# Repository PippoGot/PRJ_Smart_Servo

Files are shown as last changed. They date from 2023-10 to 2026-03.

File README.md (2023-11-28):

# Smart Servo Project
----------------------------------------------------------------

The scope of this repository is to design a new controller board for the MG996R
hobby servo, in order to improve position accuracy and performance.

In particular, the goal is to:

- Implement a more accurate position controller;

- Implement a current controller to limit stall overheating;

- Implement a I2C interface to control the servo, for:
    + current and position readings;
    + flexible and overwritable PID controller & threshold values;
    + calibration routine to estimate motor parameter;
    + possibility of daisy-chaining more servos using a limited number of ports;

More useful things to have are:

- Thermal safety shutdown;

----------------------------------------------------------------
## Folder Structure:

- "DATASHEETS": contains all of the datasheets for the components used,
both in the original controller board and in the new developed board;

- "default servo control board": contains the KiCAD files of the reverse engineered
original servo controller board;

- "MODELS & SIMULATIONS": contains the Simulink and LTSpice models, as well as the
Matlab scripts for parameters and controller tuning;

- "SOURCE": contains all the code for the microcontroller;

- "STM32 PDFs & DATASHEET": contains the documentation of the microcontroller
applied to the board, as well as some useful PDFs for making and programming
embedded projects using the microcontroller itself;

- "STM32F103C8T6 minimum board": contains the KiCAD files of a minimum board
for any embedded project using that specific microcontroller;

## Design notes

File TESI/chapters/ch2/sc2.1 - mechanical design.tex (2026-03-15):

\section{Structural Design}

The robotic leg is conceived as a three degrees of freedom (3-DOF) manipulator, a common simplification
of an insect's limb, designed to provide sufficient motion versatility within a robust and manageable structure.
The kinematic chain consists of three rigid links — Coxa, Femur, and Tibia — connected sequentially by three
revolute joints (from the robot's body toward the end-effector, as shown in Figure \ref{fig:hexapod_leg}):

\begin{itemize}
    \item \textbf{Hip Joint} ($q_1$): Connects the robot's body to the Coxa link and primarily controls the
        \textbf{yaw} motion of the leg, responsible for the lateral sweep relative to the body's longitudinal axis.
    \item \textbf{Knee Joint} ($q_2$): Connects the Coxa link to the Femur link and controls the
        \textbf{primary pitch} motion, enabling the lifting and lowering of the leg structure.
    \item \textbf{Ankle Joint} ($q_3$): Connects the Femur link to the Tibia link and controls the
        \textbf{secondary pitch} motion, significantly influencing the height and reach of the Foot (end-effector).
\end{itemize}

This configuration, is widely adopted in hexapod designs as it provides an optimal balance between complexity
and dexterity, allowing for effective gait planning and stable locomotion on various surfaces.

\begin{figure}[htbp]
    \centering
    
    \caption{Schematic Representation of the Mechanical Limb}
    \label{fig:hexapod_leg}
\end{figure}

\subsection{Limb Parametrization and Forward Kinematics}
\label{sec:dh_params}

The Denavit--Hartenberg (DH) convention \cite{denavit1955kinematic, siciliano2009robotics} is the standard
mathematical tool for describing the spatial relationships and defining the minimal parameter set required for
kinematic analysis of serial manipulators. By rigidly attaching coordinate frames to each link, DH enables a
standardized description of the link geometry and joint configuration.

The assignment of these frames follows a systematic methodology designed to isolate the four key parameters.
For a kinematic chain starting from a base frame $\{0\}$, a coordinate frame $\{i\}$ is rigidly attached to
link $i$. The most important rule is that the $z_i$-axis is placed along the axis of actuation (either
rotation or translation) for joint $i$. The $x_i$-axis is then constructed along the common normal connecting
$z_{i-1}$ (the previous joint axis) to $z_i$ (the current joint axis), with the origin of frame $\{i\}$
located at the intersection of $x_i$ and $z_i$. Finally, the $y_i$ axis is simply set to complete a
right-handed coordinate system.

Using this precise, rule-based placement of axes the entire transformation from frame $\{i\}$ to frame $\{i+1\}$
can now be described by a sequence of four fundamental operations tied directly to this geometry: the Link Length
($a_i$), Link Twist ($\alpha_i$), Link Offset ($d_i$), and the Joint Angle ($\theta_i$) (see Figure
\ref{fig:denavit_hartenberg}).

\begin{figure}[htbp]
    \centering
    
    \caption{Illustration of Denavit--Hartenberg Convention Parameters}
    \label{fig:denavit_hartenberg}
\end{figure}

The homogeneous transformation matrix, $T_{i}^{i+1}$, from frame $\{i\}$ to frame $\{i+1\}$, is given by:

\begin{equation}
    T_{i}^{i+1} = R_x(\alpha_i) \cdot T_x(a_i) \cdot R_z(\theta_i) \cdot T_z(d_i) =
    \begin{bmatrix}
        c_{\theta} & -s_{\theta} & 0 & a \\
        s_{\theta} c_{\alpha} & c_{\theta} c_{\alpha} & -s_{\alpha} & -ds_{\alpha} \\
        s_{\theta} s_{\alpha} & c_{\theta} s_{\alpha} & c_{\alpha} & dc_{\alpha} \\
        0 & 0 & 0 & 1
    \end{bmatrix}
\end{equation}

where the contracted notation $c_x = \cos(x), s_x = \sin(x)$ was used, while the overall transformation from
the base frame $\{b\}$ to the end-effector frame $\{e\}$, $T_b^e$, which is the Forward Kinematics solution,
is computed by the serial multiplication of these individual matrices:

\begin{equation}
    T_b^e = T_b^1 T_1^2 \dots T_{n-1}^n T_n^e
    \label{eqn:transf_matrix}
\end{equation}

To formally derive the Forward Kinematic model of the 3-DOF robotic limb, we apply the DH convention, following
the methodology introduced in the previous section. The assignment of the reference frames is shown in Figure
\ref{fig:assign_dh}, where the $z$-axes are represented in blue, $x$-axes in red and the $y$-axes are omitted.

Frame $\{b\}$ serves as the fixed base frame. In the context of a complete mobile hexapod, this frame is
typically attached to the center of the robot's main body to facilitate gait planning relative to the body's
center of gravity. However, for the experimental verification of the single modular limb in a benchtop setup,
frame $\{b\}$ is rigidly attached to the stationary mounting base, establishing a fixed reference for all
subsequent transformations.

\begin{figure}[htbp]
    \centering
    \begin{subfigure}[c]{0.48\textwidth}
        \centering
        
        \caption{Top View}
        \label{fig:dh_top}
    \end{subfigure}
    \hfill
    \begin{subfigure}[c]{0.48\textwidth}
        \centering
        
        \caption{Side View}
        \label{fig:dh_side}
    \end{subfigure}
    \caption{Reference Frames and DH Parameters}
    \label{fig:assign_dh}
\end{figure}

Note the following key design choices:

\begin{itemize}
    \item The base offset $d_b$ represents the distance from the base frame $\{b\}$ to the frame of the Hip Joint
        (i.e. the mounting height of the leg on the base).
    \item The link lengths $a_1$, $a_2$ and $a_3$ correspond to the length of the Coxa, Femur and Tibia links,
        respectively. These values are chosen based on a mix of aesthetics and physical constraints. More
        specifically, the Coxa length is minimized and the Femur length is chosen to be smaller than the Tibia
        length.
    \item The twist angle $\alpha_1 = 90^{\circ}$ is necessary because the axis of the Knee Joint ($z_2$) is
        orthogonal to the axis of the Hip Joint ($z_1$).
    \item Subsequent frames are coplanar, resulting in zero twist angles ($\alpha_2 = \alpha_3 = 0^{\circ}$)
        and link offsets ($d_1 = d_2 = d_3 = 0\ mm$), simplifying the transformation matrices.
    \item The joint angle $q_3$ is rotated by an extra $-180^\circ$ to simplify IK derivation and match the
        hardware implementation.
    \item Since the attitude of the end-effector is irrelevant, the final joint angle for the Tibia link is
        fixed at $\theta_4 = 0$, as the end-effector (Foot) frame $\{e\}$ is placed at the tip of the Tibia
        link, defining the final link length $a_3$.
\end{itemize}

The parameter for the DH model are reported in Table \ref{tab:dh_parameters}.

\begin{table}[htbp]
    \centering
    \begin{tabular}{c c c c c}
        \hline
        \textbf{Link} & \textbf{$a$ [mm]} & \textbf{$\alpha$ [deg]} & \textbf{$d$ [mm]} & \textbf{$\theta$ [deg]} \\
        \hline
        \hline
        Base    & $0$           & $0$   & $d_b = 178$   & $q_1$         \\
        Coxa    & $a_1 = 40$    & $90$  & $0$           & $q_2$         \\
        Femur   & $a_2 = 78$    & $0$   & $0$           & $q_3 - 180$   \\
        Tibia   & $a_3 = 132$   & $0$   & $0$           & $0$           \\
        \hline
    \end{tabular}
    \caption{Denavit--Hartenberg Parameters of the Limb}
    \label{tab:dh_parameters}
\end{table}

\subsection{Inverse Kinematics Overview and Derivation}

Forward Kinematics analysis allows for the straightforward computation of the end-effector's pose starting from a
known joint configuration. However, this direct mapping is often impractical for high-level control. Defining a
task or a trajectory is inherently more intuitive in Cartesian space (e.g. coordinates in the world frame) than
in the abstract joint space. Consequently, to command the robot to reach a specific physical location, the
inverse problem must be addressed.

Inverse Kinematics (IK) \cite{siciliano2009robotics} is the problem of determining the set of joint variables,
$q = [q_1, \dots, q_n]$, required to place the end-effector at a desired pose, $p_d = [x_d, y_d, z_d, \phi_d, \theta_d, \psi_d]^T$.
Unlike Forward Kinematics, the IK problem is fundamentally more challenging due to the non-linear relationship
between joint space and Cartesian space. The mathematical objective is to solve the inverse mapping:
\begin{equation*}
    q = f^{-1}(p_d)
\end{equation*}

The complexity of the problem stems from several factors. Solutions may be non-unique, meaning multiple
joint configurations can achieve the same end-effector pose and/or non-existent if the target pose lies outside
the robot's physical workspace. Furthermore, singularities — joint configurations that cause a loss of effective
degrees of freedom — must be avoided as they lead to control instability.

To address these challenges, solution approaches usually fall into two main categories: on one side, analytical
solutions provide closed-form, explicit equations for the joint variables as a function of the desired pose,
offering high computational efficiency and usually providing all possible solutions. They are generally preferred
for manipulators with simple geometries. Numerical Methods, conversely, use iterative algorithms to converge on a
solution by minimizing a position error function. While they are necessary for complex kinematic structures
lacking analytical solutions, they are less computationally efficient and provide only one solution per iteration.

Given the simple structure of the application, an analytical solution can be found using planar geometry and
fundamental trigonometric relationships. For the derivation, the leg geometry is conceptually separated into two
different point of views, to facilitate the calculation. Figure \ref{fig:find_ik} depicts a schematic representation
of them.

\begin{figure}[htbp]
    \centering
    \begin{subfigure}[t]{0.48\textwidth}
        \centering
        
        \caption{Top View}
        \label{fig:ik_top}
    \end{subfigure}
    \hfill
    \begin{subfigure}[t]{0.48\textwidth}
        \centering
        
        \caption{Side View}
        \label{fig:ik_side}
    \end{subfigure}
    \caption{Leg Geometry for IK Derivation}
    \label{fig:find_ik}
\end{figure}

Given a desired end-effector position $p_d = [x_d, y_d, z_d]^T$, the three required joint angles $q_1, q_2, q_3$
can be determined sequentially as follows:

\subsubsection{Joint Angle $q_1$ (Yaw)}

The first joint angle, $q_1$, is determined solely by the $X$ and $Y$ coordinates of the desired position,
representing a rotation in the horizontal plane (Figure \ref{fig:ik_top}). This is a straightforward calculation:
\begin{equation*}
    q_1 = \operatorname{atan2}(y_d,x_d)
\end{equation*}
The $\operatorname{atan2}$ function ensures that the resulting angle correctly accounts for the sign of the
coordinates across all four quadrants, providing the correct angle $\theta \in [-\pi, \pi]$.

\subsubsection{Joint Angles $q_2$ and $q_3$ (Pitch)}

The derivation of $q_2$ and $q_3$ is performed in the vertical plane (Figure \ref{fig:ik_side}),
which is defined by the Femur and Tibia links. We first define a set of auxiliary geometric variables:
\begin{itemize}
    \item \textbf{Projected Radial Distance ($r$):} The distance from the origin to the end-effector projected
        onto the $XY$-plane.
        \begin{equation*}
            r = \sqrt{x_d^2 + y_d^2}
        \end{equation*}
    \item \textbf{Horizontal Distance ($b$):} The effective horizontal distance from the $q_2$ joint axis to
        the end-effector.
        \begin{equation*}
            b = r - a_1 \Leftarrow r = b + a_1
        \end{equation*}
    \item \textbf{Vertical Distance ($h$):} The effective vertical distance from the $q_2$ joint axis to
        the end-effector.
        \begin{equation*}
            h = d_b - z_d
        \end{equation*}
    \item \textbf{Virtual Link Length ($k$):} The length of the virtual link connecting the $q_2$ joint axis
        to the end-effector, forming the third side of the triangle with links $a_2$ and $a_3$.
        \begin{equation*}
            k = \sqrt{h^2 + b^2}
        \end{equation*}
    \item \textbf{Knee Offset Angle ($\gamma)$:} The angle between the continuation of $a_1$ and the
        virtual link length $k$.
        \begin{equation*}
            \gamma = \operatorname{atan2}(h, b)
        \end{equation*}
        Using $\operatorname{atan2}$ ensures once again correctness even when $h$ is negative, i.e. when the
        Foot is above the body of the robot.
\end{itemize}

Using these auxiliary variables, the final joint angles $q_2$ and $q_3$ can now be obtained.

The second joint angle, $q_2$, is found by determining the internal angle of the $a_2, a_3, k$ triangle
using the Law of Cosines and compensating for the angle ($\gamma$):
\begin{equation*}
    q_2 = \operatorname{acos}\left(\frac{a_2^2 + k^2 - a_3^2}{2 \cdot a_2 \cdot k}\right) - \gamma
\end{equation*}
The third and final joint angle, $q_3$, is the angle between the $a_2$ and $a_3$ links. This is again derived
from the Law of Cosines:
\begin{equation*}
    q_3 = \operatorname{acos}\left(\frac{a_2^2 + a_3^2 - k^2}{2 \cdot a_2 \cdot a_3}\right)
\end{equation*}

Substituting the intermediate variables back into the expressions for $q_2$ and $q_3$ yields the final,
consolidated IK equations as a direct function of the desired end-effector coordinates as reported in Appendix
\ref{app:ik}.

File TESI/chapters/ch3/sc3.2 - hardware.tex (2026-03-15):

\section{Hardware Design and Component Selection}
\label{sec:hardware}

The design of the custom actuator module is driven by a set of strict functional and physical requirements
derived from the limitations identified in the previous section.

The most critical requirement is maintaining the exact external form factor of the original servo. This
allows for a "drop-in replacement" into the existing hexapod limb structure without mechanical modification.
Consequently, all control electronics must be miniaturized to fit within the original motor chassis volume
(approx. $40 \times 20 \times 36$ mm).

The steady-state positioning error should ideally be reduced to $<\pm 0.5^{\circ}$ to enable precise
point-to-point gait control and the control interface could shift from a time-based PWM signal to a digital bus
protocol, enabling bi-directional communication (telemetry) and flexible control, while also simplifying
scalability.

\subsubsection{Position Feedback: Magnetic Encoder (AS5600)}

To eliminate the degradation issues of resistive potentiometers, the ams AS5600 \cite{as5600} magnetic rotary
position sensor was selected. This contactless sensor measures the orientation of a diametric magnet mounted
directly on the output shaft. Key advantages include:

\begin{itemize}
    \item \textbf{Contactless Operation:} Eliminates friction and mechanical wear, significantly extending
        the operational lifespan.
    \item \textbf{High Precision:} The sensor provides a 12-bit resolution over a full rotation,
        corresponding to a theoretical precision of $0.088^{\circ}$ per step ($360^{\circ}/4096$), which is
        well above the $0.5^{\circ}$ requirement.
    \item \textbf{Digital Interface:} It communicates via a robust $\text{I}^2\text{C}$ bus, reducing the
        susceptibility to electromagnetic noise inherent in analog ADC lines within the motor housing.
\end{itemize}

\subsubsection{Power Stage: H-Bridge Driver (DRV8870)}

To drive the DC motor, the DRV8870 \cite{drv8870} was chosen for its straightforward interface and integrated
protection features. Unlike the discrete transistor bridges often found in cheap servos, this integrated
H-bridge supports up to $3.6\,\text{A}$ peak current, comfortably handling the motor's stall current. The
driver allows for:

\begin{itemize}
    \item \textbf{Bi-directional Control:} Full forward/reverse driving via logic-level inputs and internal
        shoot-through protection, automatically handling the dead-time to prevent short circuits across the
        power rails during direction changes.
    \item \textbf{PWM Speed Control:} Compatible with high-frequency switching to reduce audible noise.
    \item \textbf{Integrated Protection:} Automatic current regulation (chopping) and thermal shutdown,
        protecting the electronics from stall conditions common in legged locomotion.
\end{itemize}

\subsubsection{Control Logic: Microcontroller (STM32F103C8T6)}

The "brain" of the module is the STM32F103C8T6 \cite{stm32f103c8t6}, a 32-bit ARM Cortex-M3 microcontroller.
This component was selected for its superior computational power ($72\,\text{MHz}$), necessary to execute the
real-time control algorithms, and for its comprehensive development ecosystem.

The key peripherals are the two $I^2C$ buses used for internal and external communication and interface:

\begin{itemize}
    \item \textbf{Internal Bus:} Dedicated high-speed channel for reading the AS5600 position sensor and
        interfacing with potential future on-board peripherals (e.g. EEPROM or current sensing).
    \item \textbf{External Bus:} The main interface for the actuator module. This will allows multiple
    servos to be daisy-chained on a single bus, eliminating the need for external PWM expansion boards (e.g.
    PCA9685) and simplifying the robot's wiring harness.
\end{itemize}

Additionally, the timer/PWM peripheral will accurately control the driver module.

\subsection{PCB Design and Layout}

All selected components, along with necessary passive elements (bypass capacitors, pull-up resistors, etc...),
were integrated into a custom-designed Printed Circuit Board (PCB). To respect the strict volume constraint,
the board was designed with specific dimensions to replace the original control board inside the servo case.
Additionally, an exposed 5-pin header provides access to the SWD interface (Serial Wire Debug), allowing for
firmware flashing and real-time debugging.

Detailed schematics of the board are provided in Appendix \ref{app:pcb} while the completed design can be seen
in Figures \ref{fig:pcb_layout} and \ref{fig:motor_result}. Note that provision was made for additional future
peripheral (e.g. current sensing), although outside the scope of the current experimental validation.

\begin{figure}[htbp]
    \centering
    \begin{subfigure}[b]{0.18\textwidth}
        \centering
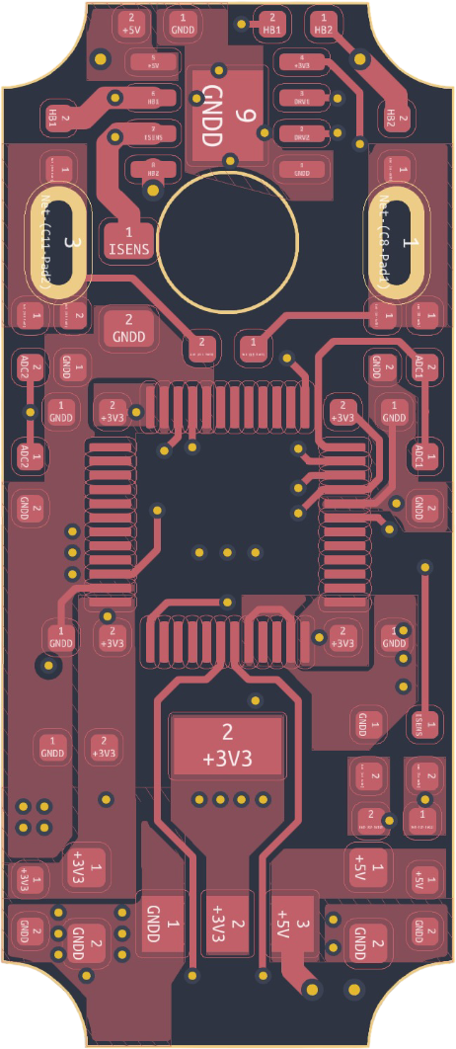
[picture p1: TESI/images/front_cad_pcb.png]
        
        \caption{CAD Front}
    \end{subfigure}
    \hfill
    \begin{subfigure}[b]{0.18\textwidth}
        \centering
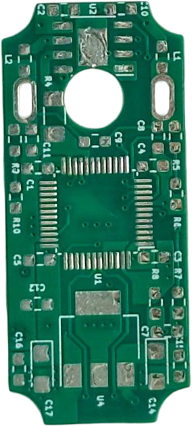
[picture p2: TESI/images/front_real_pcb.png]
        
        \caption{Real Front}
    \end{subfigure}
    \hfill
    \begin{subfigure}[b]{0.18\textwidth}
        \centering
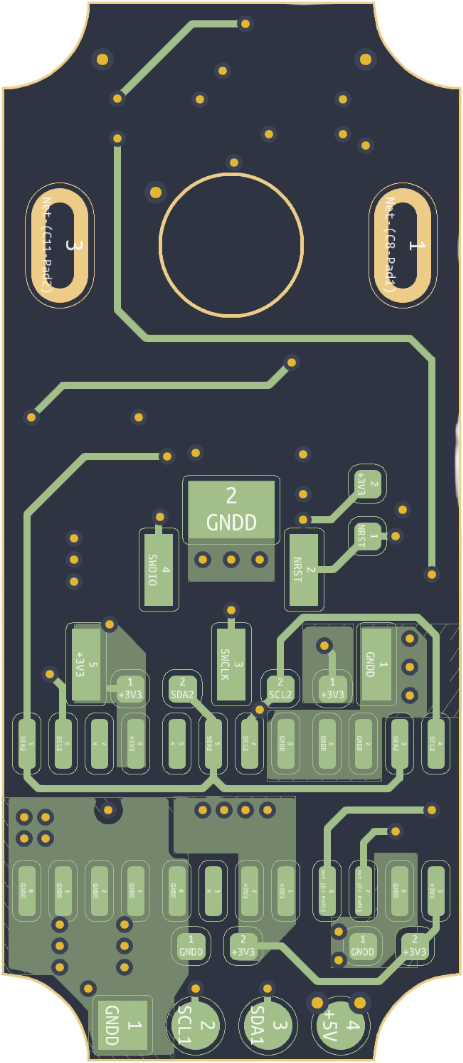
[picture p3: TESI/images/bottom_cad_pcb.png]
        
        \caption{CAD Bottom}
    \end{subfigure}
    \hfill
    \begin{subfigure}[b]{0.18\textwidth}
        \centering
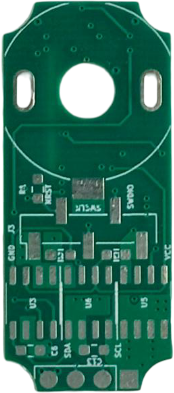
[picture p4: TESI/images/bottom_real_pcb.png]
        
        \caption{Real Bottom}
    \end{subfigure}
    \caption{Custom PCB Layout Design (CAD and Real).}
    \label{fig:pcb_layout}
\end{figure}

\begin{figure}[htbp]
    \centering
    \begin{subfigure}[b]{0.98\textwidth}
        \centering
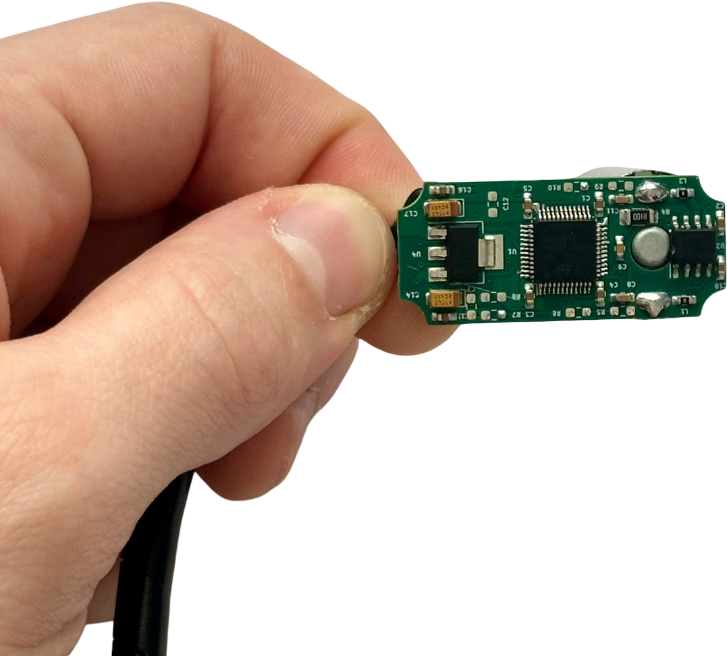
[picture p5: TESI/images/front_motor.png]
        
        \caption{Front Side}
    \end{subfigure}

    \begin{subfigure}[b]{0.98\textwidth}
        \centering
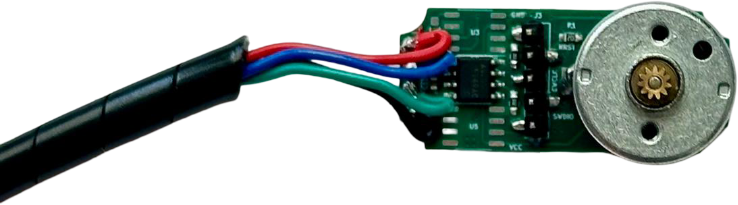
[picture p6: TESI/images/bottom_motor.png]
        
        \caption{Bottom Side}
    \end{subfigure}
    \caption{Populated Custom PCB, i.e. Smart Actuator Internals.}
    \label{fig:motor_result}
\end{figure}

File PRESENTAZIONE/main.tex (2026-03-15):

\documentclass{beamer}

\usepackage[T1]{fontenc}
\usepackage[utf8]{inputenc}
\usepackage[english]{babel}
\usepackage{lmodern}
\usepackage{graphicx}
\usepackage{wrapfig}
\usepackage{animate}

% Use Unipd as theme, with options:
% - pageofpages: define the separation symbol of the footer page of pages (e.g.: of, di, /, default: of)
% - logo: position another logo near the Unipd logo in the title page (e.g. department logo), passing the second logo path as option
% Use the environment lastframe to add the endframe text
\usetheme[pageofpages = of]{Unipd}

\title[]{Hardware/Software Design and Implementation of an Open Robotic Chain Using Custom Servo-Motor Modules}
\subtitle{}
\author[Filippo Gottardo]{ % Argomento opzionale per il piè di pagina
    \texorpdfstring{ % Inizio comando magico
        % --- VERSIONE GRAFICA (per la slide) ---
        \parbox{\linewidth}{
            % Colonna Sinistra: Relatori
            \begin{minipage}[t]{0.5\linewidth}
                \raggedright
                \footnotesize
                \textbf{Supervisor:}\\
                Prof. Angelo Cenedese\\[0.5em]
                \textbf{Co-supervisor:}\\
                Ing. Riccardo Antonello
            \end{minipage}%
            \hfill
            % Colonna Destra: Candidato
            \begin{minipage}[t]{0.45\linewidth}
                \raggedleft
                \textbf{Candidate:}\\
                Filippo Gottardo
            \end{minipage}
        }
    }{Filippo Gottardo} % --- VERSIONE TESTO (per i metadati PDF, invisibile) ---
}

\date{December 4, 2025}

\begin{document}

% Make the title page
\frame{\titlepage}

% Insert the general toc
\begin{frame}{Table of Contents}
    \tableofcontents
\end{frame}

\section{Thesis Objective}

    \begin{frame}{Thesis Objectives}
        \begin{columns}[c]
            \begin{column}{0.5\textwidth}
                \centering
                Design and implement a 3-DOF robotic limb for a bio-inspired walking hexapod.

                \vspace{10pt}
                \textbf{Tracking accuracy}

                \vspace{10pt}
                \textbf{Accessible budget}

                \vspace{10pt}
                \textbf{Modular design}
            \end{column}

            \begin{column}{0.50\textwidth}
                \centering
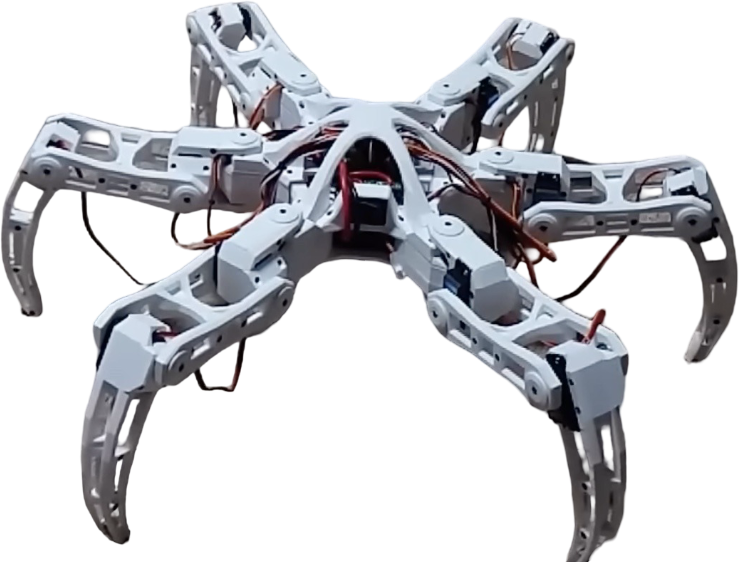
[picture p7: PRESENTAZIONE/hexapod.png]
                
            \end{column}
        \end{columns}
    \end{frame}

\section{Actuator Module}

    \begin{frame}{Commercial Actuator}
        \begin{columns}[c]
            \begin{column}{0.5\textwidth}
                \centering
                \textbf{MG996R servo motor}
                \vspace{10pt}
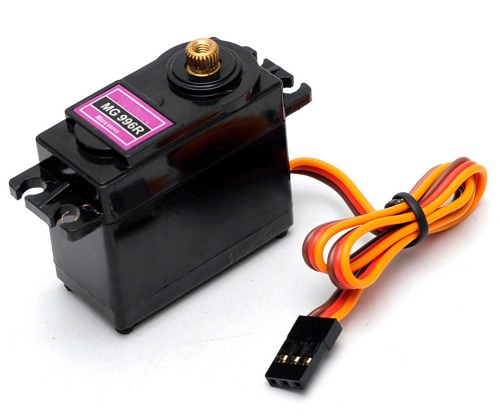
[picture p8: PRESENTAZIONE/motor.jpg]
                

                Non-linear
                \vspace{10pt}

                Backlash/Hysteresis
                \vspace{10pt}

                $\theta_A(T_{on})\ne\theta_B(T_{on})$
                \vspace{10pt}

                No access to $\theta$

            \end{column}

            \begin{column}{0.50\textwidth}
                \centering
                
                
            \end{column}
        \end{columns}
    \end{frame}

    \begin{frame}{Custom Redesign}
        \centering
        HW/SW Redesign
        \begin{columns}[b]
            \begin{column}{0.50\textwidth}
                \centering
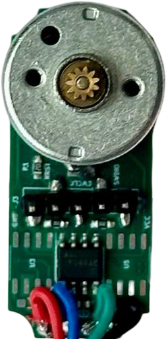
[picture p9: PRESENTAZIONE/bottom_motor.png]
                % <--- Importante questo %
                \hfill
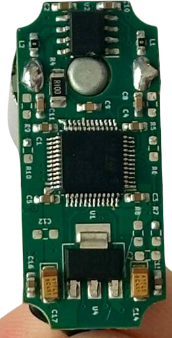
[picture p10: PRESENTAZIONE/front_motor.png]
                

                Potentiometer $\Rightarrow$ Magnetic Encoder
                \vspace{10pt}

                STM32 Microcontroller
            \end{column}

            \begin{column}{0.5\textwidth}
                \centering
                

                Switching PID
                \vspace{10pt}

                PWM signal $\Rightarrow I^2C$ Bus Protocol
            \end{column}
        \end{columns}
    \end{frame}

    \begin{frame}{Switching PID}
        \begin{columns}[c]
            \footnotesize
            \begin{column}{0.5\textwidth}
                \centering
                Generalized Position Error: $\sigma = K_I(\theta_d - \theta)$\\

                \vspace{20pt}
                Controller State: $\phi = K_P(\theta_d - \theta) + \frac{K_I \sigma}{s}$\\

                \vspace{20pt}
                Controller Output: $u = \phi - K_Dv$\\

                \vspace{20pt}
                $K_P, K_I > 0, K_PK_D > K_I$\\

                \vspace{20pt}
                $[K_P, K_I, K_D]^T = [10, 0.9, 0.1]^T$
            \end{column}

            \begin{column}{0.5\textwidth}
                \centering
                During stick phase, $v = 0, \sigma(t) = \sigma, -F_- \le \phi \le +F_+$.\\

                \vspace{20pt}
                Integral action $\phi$ accumulates energy to overcome static friction.\\

                \vspace{20pt}
                Once motion begins, if the position errors surpasses the set-point, $\phi \gets -\phi$.\\
            \end{column}
        \end{columns}

        \vspace{20pt}

        \tiny
        "To stick or to slip: A reset PID control perspective on positioning systems with friction"\\
        A. Bisoffi, R. Beerens, W. Heemels, H. Nijmeijer, N. van de Wouw, and L. Zaccarian\vspace{10pt}

        "Switching pid strategy for positioning systems with non-symmetric friction and noisy velocity measurements"\\
        R. Lorigiola, T. Borzone, M. Bruschetta, and A. Cenedese
    \end{frame}

    \begin{frame}{Redesign Results}
        \begin{columns}[c]
            \begin{column}{0.38\textwidth}
                \centering
                
                
            \end{column}
            \begin{column}{0.24\textwidth}
                \centering\footnotesize
                Improvements on:\vspace{10pt}

                Linearity\vspace{10pt}

                Operative Range\vspace{10pt}

                Backlash/Hysteresis\vspace{20pt}

                Micro-scale adjustments without limit cycles\vspace{10pt}

                Settling error $e_\theta \le \pm 1^\circ$
            \end{column}
            \begin{column}{0.38\textwidth}
                \centering
                
                
            \end{column}
        \end{columns}
    \end{frame}

    \begin{frame}{Redesign Metrics}
        \centering
        

        Price per unit $\le$ 8€ (including components, PCB and shipping)
    \end{frame}

\section{Robotic Limb}

    \begin{frame}{Robotic Limb Design}
        \begin{columns}[c]
            \begin{column}{0.5\textwidth}
                \centering
                

                Forward Kinematics\vspace{10pt}

                Inverse Kinematics\vspace{10pt}

                Reachable Workspace
            \end{column}

            \begin{column}{0.50\textwidth}
                \centering
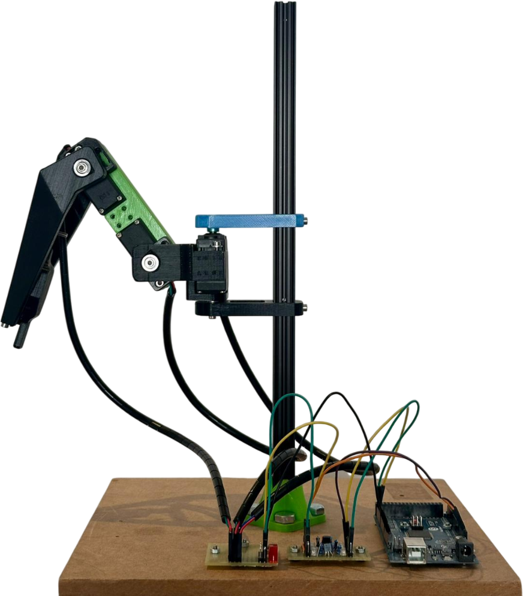
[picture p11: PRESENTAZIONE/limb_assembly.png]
                \reflectbox{}
            \end{column}
        \end{columns}
    \end{frame}

    \begin{frame}{Path Generation}
        \begin{columns}[c]
            \begin{column}{0.50\textwidth}
                Assuming \textbf{Flat Ground}\vspace{10pt}

                Geometric derivation parametrized w.r.t. walking speed and direction\vspace{10pt}

                \textbf{Stance Phase:}\\
                Propulsion and constant speed\vspace{10pt}

                \textbf{Swing Phase:}\\
                Repositioning of the foot with no jumps in accelerations
            \end{column}

            \begin{column}{0.5\textwidth}
                \centering
                
            \end{column}
        \end{columns}
    \end{frame}

    \begin{frame}{Simulation and HIL}
        \centering
        Hardware in the Loop Control Chain\vspace{10pt}

        

        Simulation Control Chain\vspace{10pt}

        
    \end{frame}

    \begin{frame}{Robotic Limb Design}
        \begin{columns}[c]
            \begin{column}{0.5\textwidth}
                \centering
                \footnotesize
                Simulation model $\approx$ Physical model\vspace{20pt}

                
            \end{column}

            \begin{column}{0.50\textwidth}
                \centering
                % Sintassi: \animategraphics[opzioni]{fps}{percorso/prefisso_nome}{inizio}{fine}
                % loop: ripete all'infinito
                % autoplay: parte appena apri la slide
                % width: larghezza

                \animategraphics[loop, autoplay, width=0.9\textwidth]{20}{experiment/ezgif-frame-}{002}{045}
                % Spiegazione parametri:
                % {10} = Frame al secondo (velocità)
                % {animazione/bot_} = Cerca file tipo "animazione/bot_0.png", "bot_1.png"...
                % {001}{101} = Dal frame numero 1 al numero 101
                (2x)
            \end{column}
        \end{columns}
    \end{frame}

    \begin{frame}{Error Metrics}
        \begin{columns}[c]
            \begin{column}{0.4\textwidth}
            \centering
            Change in \textbf{amplitude} but similar \textbf{shape}, suggesting higher \textbf{tracking delay} in the experiment and \textbf{inertia} effects in both.\vspace{10pt}\\

            Notice the scaling of the simulation error\\(factor of 10)
            \end{column}

            \begin{column}{0.6\textwidth}
            \centering
                
                
            \end{column}
        \end{columns}
    \end{frame}

    \begin{frame}{Path Adaptation 1/2}
        \begin{columns}[c]
            \begin{column}{0.4\textwidth}
            \centering
            Relaxing the flat ground assumption\vspace{20pt}

            Contact sensor in the Foot\\+\\Adaptive FSM\\Path Generator\vspace{20pt}
            \end{column}

            \begin{column}{0.6\textwidth}
            \centering
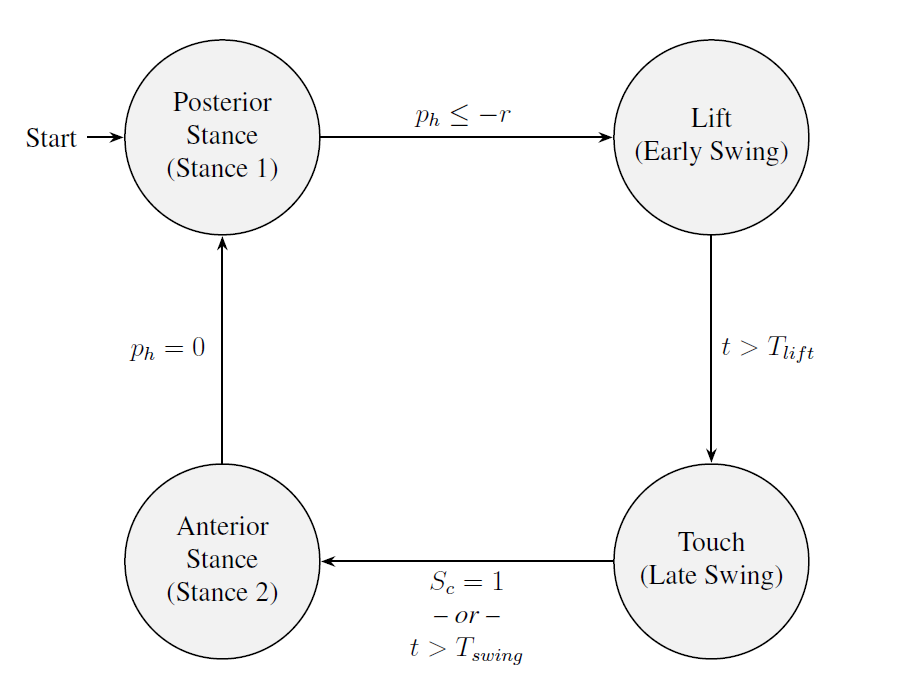
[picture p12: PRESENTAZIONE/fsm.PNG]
                
            \end{column}
        \end{columns}
    \end{frame}

    \begin{frame}{Path Adaptation 2/2}
        \begin{columns}[c]
            \begin{column}{0.5\textwidth}
                \centering
                \footnotesize
                
            \end{column}

            \begin{column}{0.50\textwidth}
                \centering
                % Sintassi: \animategraphics[opzioni]{fps}{percorso/prefisso_nome}{inizio}{fine}
                % loop: ripete all'infinito
                % autoplay: parte appena apri la slide
                % width: larghezza

                \animategraphics[loop, autoplay, width=\textwidth]{10}{animation/ezgif-frame-}{001}{101}
                % Spiegazione parametri:
                % {10} = Frame al secondo (velocità)
                % {animazione/bot_} = Cerca file tipo "animazione/bot_0.png", "bot_1.png"...
                % {001}{101} = Dal frame numero 1 al numero 101
            \end{column}
        \end{columns}
    \end{frame}

\section{Conclusions}

    \begin{frame}{Final Considerations}
        Complete design of the 3-DOF robotic limb, from micro-scale components (custom actuator) to macro-scale system (full limb), including the control chain.\vspace{10pt}

        Excellent results with a contained budget, also applicable to similar projects.\vspace{10pt}

        Solid foundations for future improvements:
        \begin{enumerate}
            \item Automatic controller gain tuning;
            \item Full robot  assembly;
            \item Adaptive path generator testing and refinement;
        \end{enumerate}
    \end{frame}

    \begin{emptyframe}
        Thank you!\\Questions?
    \end{emptyframe}

\section*{Extra}

    \begin{frame}{Metrics}
        \centering
        $$\text{RMSE} = \sqrt{ \frac{1}{N} \sum_{i=1}^{N} \left( y_{meas}[i] - y_{ideal}[i] \right)^2 }$$

        $$E_{max} = \max_{i} \left| y_{meas}[i] - y_{ideal}[i] \right|$$

        $$\mathcal{A}_{hyst} = \int_{x_{min}}^{x_{max}} \left| \left( y_{fwd}(x) - y_{bwd}(x) \right) \right|\, dx $$

        $$H_{avg} = \frac{\mathcal{A}_{hyst}}{x_{max} - x_{min}}$$
    \end{frame}

\end{document}

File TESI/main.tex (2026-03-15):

% le caratteristiche richieste dall'università sono elencate qui: https://stem.elearning.unipd.it/mod/book/view.php?id=234&chapterid=46#modalita
% 12pt: font richiesto dall'università
% twoside: i margini interni ed esterni sono scambiati per le pagine "a sinistra" e "a destra"
% openright: i capitoli cominciano in pagine dispari ("a destra")
% extreport: supporta 12pt
\documentclass[12pt, a4paper, twoside, openright]{extreport}

% --- PACCHETTI ---

% margini
\usepackage{geometry}
\geometry{a4paper, top = 2cm, bottom = 2cm, outer = 2cm, inner = 3cm, includeheadfoot}

% unità di misura e matematica
\usepackage{siunitx, amsmath}
%\everydisplay{\footnotesize}
\everymath{\displaystyle}

% numerazione capitoli e formato titolo
\usepackage[english]{babel}
\usepackage{titlesec}
\titleformat{\chapter}[hang]                % titolo + numero sulla stessa linea
    {\normalfont\huge\bfseries}             % stile del titolo
    {\thechapter.}                          % numero del capitolo
    {1em}                                   % spazio tra numero e titolo
    {}                                      % codice prima del testo
\titlespacing*{\chapter}{0pt}{-10pt}{20pt}  % margini e spazi verticali

% didascalie
\usepackage{subcaption, caption}

% impaginazione
\usepackage{setspace}
\onehalfspacing
\setlength{\parindent}{0pt} % niente rientro nei paragrafi
\setlength{\parskip}{0.7em} % spazio tra paragrafi

\usepackage{enumitem}
\setlist{itemsep = 0.25em, topsep = 0.25em} % spazio tra elementi di una lista

\usepackage{tocloft} % 1. Carica il pacchetto
\setlength{\cftbeforechapskip}{20pt}

% font
\usepackage{times}

% colori, grafiche e tabelle
\usepackage[utf8]{inputenc}
\usepackage[T1]{fontenc}
\usepackage{booktabs}   % Per linee orizzontali professionali
\usepackage{longtable}  % Per tabelle che possono andare su più pagine
\renewcommand{\arraystretch}{1.3} % Aumenta leggermente lo spazio tra le righe
\usepackage[dvipsnames]{xcolor} % Per colori avanzati (opzionale, ma utile)
\usepackage{graphicx}
\usepackage{wrapfig}
\usepackage{tikz}
\usetikzlibrary{automata, positioning, arrows.meta, bending}
\usepackage{algorithm}
\usepackage{algpseudocode}
\usepackage{calc} % Serve per calcolare la larghezza della colorbox

% import/export formato pdf
\usepackage{pdfpages}
\usepackage[a-1a]{pdfx}
\hypersetup{hidelinks} % nascondi rettangoli di href

% bibliografia e appendice
\usepackage{csquotes, url}
\usepackage[backend = biber, style = ieee]{biblatex}
\addbibresource{bibliography.bib}
\usepackage[toc,page]{appendix}

% macro personalizzate

% --- PACCHETTI PER AMBIENTE TODO ---
\usepackage[breakable]{tcolorbox}

% --- DEFINIZIONE AMBIENTE TODO ---
% Crea un nuovo ambiente tcolorbox chiamato 'todo'
\newtcolorbox{todo}{
    colback   = red!5!white,  % Colore di sfondo (rosa = rosso 5% + bianco 95%)
    colframe  = red!75!black, % Colore del bordo (rosso scuro)
    fonttitle = \bfseries,    % Titolo in grassetto
    title     = {TODO:},      % Titolo automatico
    breakable = true,         % Permette al box di spezzarsi tra le pagine
    arc       = 2mm,          % Angoli leggermente arrotondati
    boxrule   = 0.5mm,        % Spessore del bordo
}

% --- MACRO PER SEGNAPOSTO IMMAGINE ---
% Crea un box segnaposto per una figura
% Argomenti:
% #1: label (per \ref)
% #2: didascalia (per \caption)
% #3: Testo principale (grassetto)
% #4: Descrizione (corsivo)
\newcommand{\segnaposto}[4]{%
    \begin{figure}[htbp]
    \centering
    \framebox{\parbox{0.6\textwidth}{\centering
        \vspace{3cm} % Spazio sopra
        \textbf{#3} \\
        \small\textit{#4}
        \vspace{3cm} % Spazio sotto
    }}
    \caption{#2}
    \label{#1}
    \end{figure}
}

% --- DEFINIZIONE MACRO PER I BLOCCHI COLORATI ---
% Sintassi: \ColorBlock{ColoreSfondo}{Contenuto}
\newcommand{\ColorBlock}[2]{%
    \State \makebox[\linewidth][l]{%
        \colorbox{#1!15}{% !15 rende il colore molto tenue (pastello)
            \parbox{\dimexpr\linewidth-2\fboxsep}{#2}%
        }%
    }%
}

% --- DOCUMENTO PRINCIPALE ---

% --- FRONTESPIZIO ---
\title{Hardware/Software Design and Implementation\\of an Open Robotic Chain\\Using Custom Servo-Motor Modules}
\author{Gottardo Filippo}
\date{04/12/2025}
\newcommand{\supervisor}{Prof. Cenedese Angelo}
\newcommand{\cosupervisor}{Ing. Antonello Riccardo}

% inizio del documento
\begin{document}
    \pagenumbering{Roman}
    \pagestyle{empty}
    \input{chapters/ch0/frontespizio.tex}
    \pagestyle{plain}
    \cleardoublepage

    % --- ABSTRACT ---
    \input{chapters/ch0/abstract.tex}

    % --- INDICE ---
    \cleardoublepage
    \tableofcontents
    \cleardoublepage
    \pagenumbering{arabic}
    %\input{chapters/content mockup.tex}     % mockup del contenuto

    % --- CAPITOLI ---
    \input{chapters/ch1/ch1 - intro.tex}
    \input{chapters/ch2/ch2 - model.tex}
    \input{chapters/ch3/ch3 - servomotor.tex}
    \input{chapters/ch4/ch4 - prototype.tex}
    \input{chapters/ch5/ch5 - conclusions.tex}
    \input{chapters/ch5/ch6 - acknowledgements.tex}
    \cleardoublepage

    % --- APPENDICI ---
    \appendix
    \include{chapters/appendices/appendix.tex}

    % --- BIBLIOGRAFIA ---
    \printbibliography[heading = bibintoc, title = {References}]

\end{document}

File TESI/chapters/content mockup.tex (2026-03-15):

\chapter{Introduction}

\chapter{Methodologies, Design and Simulation}
    \section{Mechanical Design}
        \subsection{Denavit--Hartenberg Overview}
        \subsection{Limb Parametrization and Forward Kinematics}
        \subsection{Inverse Kinematics Overview and Derivation}
    \section{Workspace and Path Planning}
        \subsection{Workspace Definition and Analysis}
        \subsection{Trajectory Design}
    \section{Control and Simulation}
        \subsection{Open Loop Control Strategy}
        \subsection{Digital Simulation Setup}
        \subsection{Results}
    \section{Proprioception and Path Adaptation}
        \subsection{Contact Sensing and Architectuaral Shift}
        \subsection{Finite State Trajectory Generator}
        \subsection{Adaptive Simulation Results}

\chapter{Custom Smart Actuator Module Design}
    \section{Limitations of Commercial Servos}
    \section{Hardware Design and Component Selection}
        \subsection{Requirements Definition}
        \subsection{Components Selection}
        \subsection{PCB Design and Layout}
    \section{Embedded Software Architecture}
        \subsection{Control Strategy}
    \section{Module Characterization and Benchmarking}
        \subsection{Static Analysis: Linearity and Hysteresis}
        \subsection{Step Response Analysis: Response and Precision}
        \subsection{Results Summary}

\chapter{Prototype Implementation}
    \section{Hardware-in-the-Loop Architecture}
        \subsection{Limb Assembly}
        \subsection{Simulink Setup}
        \subsection{Arduino Setup}
    \section{Performance Assessment}

\chapter{Conclusions}
    \section{Achievements and Considerations}
    \section{Economical and Practical Aspects}
    \section{General Applicability and Future Work}

\chapter{Acknowledgements}
    \section{AI Fair Use}
    \section{Ringraziamenti}

% --- Appendices ---
\appendix
\chapter{Appendix}

% --- Bibliography ---
\addcontentsline{toc}{chapter}{Bibliography}

\begin{thebibliography}{99}

\end{thebibliography}

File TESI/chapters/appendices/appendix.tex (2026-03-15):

\chapter{Appendix}

\newpage
\section{Full Inverse Kinematics Expressions}
\label{app:ik}

{\footnotesize\begin{align}
    q_1 &= \operatorname{atan2}(y_d, x_d)
    \\[3ex]
    q_2 &= \operatorname{acos}\left(\frac{a_2^2 - a_3^2 + \left(\sqrt{x_d^2 + y_d^2} - a_1\right)^2 + (d_b - z_d)^2}
    {2 \cdot a_2 \cdot \sqrt{\left(\sqrt{x_d^2 + y_d^2} - a_1\right)^2 + (d_b - z_d)^2}}\right) -
    \operatorname{atan2}\left((d_b - z_d), \left(\sqrt{x_d^2 + y_d^2} - a_1\right)\right)
    \\
    q_3 &= \operatorname{acos}\left(\frac{a_2^2 + a_3^2 - \left(\sqrt{x_d^2 + y_d^2} - a_1\right)^2 - (d_b - z_d)^2}
    {2 \cdot a_2 \cdot a_3}\right)
    \label{eqn:inverse_kinematics}
\end{align}}

\newpage
\section{Servo Module Schematic}
\label{app:pcb}

\begin{figure}[htb]
    \centering
    
\end{figure}

\newpage
\section{Software Architecture}
\label{app:software}

\begin{figure}[htb]
    \centering
    
\end{figure}

\newpage
\section{Register Map}
\label{app:register}

\begin{longtable}{@{} l l l l l @{}}
\caption{System Register Map} \\

% --- Intestazione Prima Pagina ---
\toprule
\textbf{Addr} & \textbf{Register Name} & \textbf{Data Type} & \textbf{Group} & \textbf{Default} \\
\midrule
\endfirsthead

% --- Intestazione Pagine Successive ---
\toprule
\textbf{Addr} & \textbf{Register Name} & \textbf{Data Type} & \textbf{Group} & \textbf{Default} \\
\midrule
\endhead

% --- Footer Pagine Intermedie ---
\midrule
\multicolumn{5}{r}{\textit{Continued...}} \\
\bottomrule
\endfoot

% --- Footer Finale ---
\bottomrule
\endlastfoot

% --- CONTENUTO ---

% SW-PID Controller (Tipi dedotti da DefaultSettings: float)
\texttt{0x00} & ProportionalGain   & \texttt{float}    & SWPID Control & $10.0f$ \\
\texttt{0x01} & IntegralGain       & \texttt{float}    & SWPID Control & $0.9f$ \\
\texttt{0x02} & DerivativeGain     & \texttt{float}    & SWPID Control & $0.1f$ \\
\texttt{0x03} & AntiwindupMax      & \texttt{float}    & SWPID Control & $5.0f$ \\
\texttt{0x04} & AntiwindupMin      & \texttt{float}    & SWPID Control & $-5.0f$ \\
\texttt{0x05} & OutputMax          & \texttt{float}    & SWPID Control & $1.0f$ \\
\texttt{0x06} & OutputMin          & \texttt{float}    & SWPID Control & $-1.0f$ \\
\addlinespace

% Servo Motor State (Non presenti in Default, ipotizzo float per coerenza)
\texttt{0x20} & DesiredPosition    & \texttt{int32\_t}  & Servo State & 0 \\
\texttt{0x21} & ActualPosition     & \texttt{int32\_t}  & Servo State & - \\
\texttt{0x22} & PositionOffset     & \texttt{int32\_t}  & Servo State & -2048 \\
\texttt{0x26} & DutyCycle          & \texttt{int32\_t}  & Servo State & - \\
\addlinespace

% AS5600 (Tipi dedotti: uint16_t)
\texttt{0x40} & ZeroPosition       & \texttt{uint16\_t} & AS5600     & \texttt{0x000} \\
\texttt{0x41} & StopPosition       & \texttt{uint16\_t} & AS5600     & \texttt{0xFFF} \\
\addlinespace

\end{longtable}

\newpage
\section{Metrics Formulae}
\label{app:metrics}

\textbf{Root Mean Square Error (RMSE)}
$$\text{RMSE} = \sqrt{ \frac{1}{N} \sum_{i=1}^{N} \left( y_{meas}[i] - y_{ideal}[i] \right)^2 }$$

This metric quantifies the standard deviation of the residuals between the measured output ($y_{meas}$) and the ideal
theoretical reference ($y_{ideal}$). It serves as the primary indicator of the system's overall linearity accuracy,
aggregating the error over the entire dataset.

\textbf{Maximum Absolute Error}
$$E_{max} = \max_{i} \left| y_{meas}[i] - y_{ideal}[i] \right|$$

Represents the worst-case deviation observed across the entire operating range. It identifies the single instance
where the actuator's position diverged most significantly from the expected ideal value.

\textbf{Hysteresis Loop Area}
$$\mathcal{A}_{hyst} = \left| \int_{x_{min}}^{x_{max}} \left( y_{fwd}(x) - y_{bwd}(x) \right) \, dx \right|$$

Calculated via numerical integration (trapezoidal rule), this value represents the total area enclosed between the
forward ($y_{fwd}$) and backward ($y_{bwd}$) trajectories. It quantifies the cumulative effect of mechanical backlash,
friction, and sensor noise over a full motion cycle.

\textbf{Average Hysteresis Error}
$$H_{avg} = \frac{\mathcal{A}_{hyst}}{x_{max} - x_{min}}$$

This metric normalizes the hysteresis area by the input signal range ($x_{max} - x_{min}$). It provides the average
magnitude of the hysteresis gap in degrees, allowing for a direct and fair comparison between systems operating on
different input domains.

\newpage
\section{Bill of Material}
\label{app:bom}

Bill of Materials (BOM) for a single custom actuator module. Prices reflect the per-unit cost derived from bulk purchases
on third-party websites and are comprehensive of shipping.

\begin{table}[htbp]
    \centering
    \begin{tabular}{lccc}
        \toprule
        \textbf{Component}  & \textbf{Qty} & \textbf{Bulk Price Reference} & \textbf{Unit Cost (€)} \\
        \midrule
        Custom PCB                              & 1             & 6.18€ / 10 pcs    & 0.62 \\
        STM32F103C8T6 (MCU)                     & 1             & 7.99€ / 10 pcs    & 0.80 \\
        AS5600 (Magnetic Sensor)                & 1             & 4.42€ / 5 pcs     & 0.88 \\
        DRV8870 (Motor Driver)                  & 1             & 2.20€ / 10 pcs    & 0.22 \\
        Tantalum Cap. (100 $\mu$F)              & 2             & 1.47€ / 10 pcs    & 0.29 \\
        AMS1117 (LDO Regulator)                 & 1             & 2.16€ / 50 pcs    & 0.04 \\
        SMD Passives (0603 R/C)                 & $\approx$30   & Lump sum          & 0.25 \\
        MG996R Servo Motor\textsuperscript{*}   & 1             & 20.39€ / 5 pcs    & 4.08 \\
        \midrule
        \textbf{Total Cost per Module} & & & \textbf{7.18} \\
        \bottomrule
    \end{tabular}
    \vspace{1ex}

    {\footnotesize \textsuperscript{*}Current market price (2025). Using older stock (2018), the motor unit cost was
    $\approx 1.92$€, lowering the total to $\approx 5.02$€.}
\end{table}

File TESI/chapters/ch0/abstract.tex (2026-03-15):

\chapter*{Abstract}
\addcontentsline{toc}{chapter}{Abstract}

This thesis presents a comprehensive, top-down engineering approach to the design and control of a modular robotic
limb for a hexapod platform. The primary objective is to overcome the performance limitations inherent in low-cost
commercial actuation, which typically hinder precise legged locomotion.

The research begins with the kinematic modeling and digital simulation of the limb in the MATLAB/Simulink environment,
establishing a simulation model to validate trajectory planning and inverse kinematics algorithms. The core contribution
of this work is the development of a novel, custom "Smart Actuator" module designed to replace standard hobbyist
servo-motors. This custom embedded solution integrates a high-resolution magnetic encoder, a high-current H-bridge
driver, and an STM32 microcontroller. Crucially, it implements a non-linear Switching PID control strategy specifically
tuned to mitigate stick-slip friction phenomena and mechanical backlash.

The system is validated through a Hardware-in-the-Loop (HIL) architecture, bridging the simulation environment with the
physical prototype. Experimental benchmarking demonstrates a dramatic improvement in performance.

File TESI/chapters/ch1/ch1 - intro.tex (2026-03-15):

\chapter{Introduction}

The field of bio-inspired robotics \cite{delcomyn2004insect} has seen rapid advancements in recent years,
\cite{chai2022survey,fan2024review} driven by the need for autonomous systems capable of navigating
unstructured and complex environments. Among these, hexapod robots offer a unique combination of stability,
payload capacity, and terrain adaptability that wheeled platforms cannot match. However, the effective deployment
of such legged systems is fundamentally dictated by the quality of their actuation.

\subsubsection{Motivation and Problem Statement}

Precise legged locomotion requires accurate control of joint angles and torque. While industrial-grade actuators
(e.g. Dynamixel-X series \cite{robotis_dynamixel_x}) offer the necessary fidelity and communication interfaces,
their prohibitive cost makes them inaccessible for many research and prototyping applications. Conversely,
low-cost "hobby" servo-motors, while affordable, present critical limitations. They typically operate as
"black boxes" with inaccessible internal control loops, rely on wear-prone resistive potentiometers for feedback,
and suffer from significant deadbands and non-linear friction effects.

\subsubsection{Thesis Objectives}

This thesis addresses these challenges by proposing a comprehensive hardware-software design. The overarching goal
is to bridge the gap between low-cost hardware and high-performance control. The specific objectives are:

\begin{enumerate}
    \item \textbf{Kinematic Framework:} To derive and validate the mathematical model of a 3-DOF hexapod limb,
        ensuring reliable workspace analysis and trajectory planning.
    \item \textbf{Actuator Redesign:} To engineer a custom "Smart Actuator" module that retains the standard form factor
        of commercial servos but upgrades performances through internal electronics replacements.
    \item \textbf{Sim-to-Real Validation:} To establish a Hardware-in-the-Loop (HIL) architecture that allows for direct
        performance comparison between a theoretical numerical model and the physical prototype.
    \item \textbf{Modular Scalability:} To adopt a strictly modular design philosophy for both hardware and software
        architectures, ensuring that the single-leg system can be seamlessly replicated and integrated to realize the
        complete hexapod robot in future developments.
\end{enumerate}

\subsubsection{Thesis Structure}

The remainder of this thesis is organized as follows:

\begin{itemize}
    \item Chapter \ref{ch:model} establishes the theoretical foundation. It details the mechanical design of the limb,
        the Denavit--Hartenberg parameterization, and the Inverse Kinematics derivation. It also presents the
        numerical model developed in Simscape Multibody, which serves as reference for validation.
    \item Chapter \ref{ch:servomotor} focuses on the component-level engineering. It analyzes the limitations of
        commercial servos and details the hardware and software design of the custom actuator module, including the
        Switching PID control algorithm, ultimately evaluating the achieved improvements.
    \item Chapter \ref{ch:prototype} describes the system integration and experimental validation. It outlines the
        Hardware-in-the-Loop architecture and presents a quantitative comparison of the trajectory tracking performance
        between the simulation and the physical prototype.
    \item Chapter \ref{ch:conclusions} concludes the thesis by summarizing the achieved results, and outlining future
        research directions.
\end{itemize}

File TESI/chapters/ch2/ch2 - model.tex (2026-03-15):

\chapter{Model Design and Simulation}
\label{ch:model}

This chapter illustrates the theoretical steps of design, control and simulation of the robotic system. The analysis
deliberately focuses on the developement of a single leg of a hexapod robot.

This strategic choice adheres to a modular approach, which is convenient for several reasons.
Firstly, it ensures that the design can be easily extended and replicated for the remaining limbs, simplifying
the eventual future assembly of the complete robot. Secondly, isolating the study to a single leg allows for a
concentrated focus on the fundamental kinematic and control aspects, thereby optimizing the analysis and
limiting system complexity and implementation time.

\input{chapters/ch2/sc2.1 - mechanical design.tex}
\input{chapters/ch2/sc2.2 - trajectory.tex}
\input{chapters/ch2/sc2.3 - control and simulation.tex}
\input{chapters/ch2/sc2.4 - proprioception.tex}

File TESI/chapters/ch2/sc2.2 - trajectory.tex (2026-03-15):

\section{Reachable Workspace and Path Planning}
\label{sec:trajectory}

Following the developement of the limb's kinematic model, the next logical step is to verify the correctness of
the design and its behaviour through digital simulation. However, two preliminary steps are essential: the reachable
workspace of the system must be analyzed to understand its operational boundaries and a desired trajectory for the
end-effector must be designed.

\subsection{Workspace Definition and Analysis}

The reachable workspace of a manipulator is formally defined as the complete set of all Cartesian positions
$p = [x,y,z]^{T}$ that its end-effector can attain, given the physical constraints of its kinematic
chain \cite{ding2010locomotion}. It represents the entire volume of space accessible to the robot's
end-effector. For this 3-DOF limb, the workspace is determined by the three link lengths ($a_{1},a_{2},a_{3}$)
and, most critically, by the actuation limits imposed on its three joints ($q_{1},q_{2},q_{3}$).

To characterize this 3D volume, a two-stage approach is taken. First, the 2D planar workspace is analyzed.
This is done by fixing the Hip Joint at a neutral angle (e.g. $q_1 = \ang{0}$) and generating the boundary of
the leg's reach in a single vertical plane. A 2D cross-section is then obtained by sweeping the Knee
($q_2$) and Ankle ($q_3$) joints through their entire operational ranges. The resulting surface (Figure
\ref{fig:workspace_analysis}) is finally revolved around the Hip joint axis by sweeping $q_1$ through its own
range, thereby generating the final 3D reachable volume.

\begin{figure}[htbp]
    \centering
    
    \caption{Reachable Workspace Section for $q_1 = 0$}
    \label{fig:workspace_analysis}
\end{figure}

The actuator limits are the primary constraints defining this space. These limits are imposed both by the
physical components (i.e. the finite rotational range of the servo-motors) and by the mechanical design itself,
which is configured to prevent self-collision between links and other limbs.
For this specific implementation, the joint constraints are defined as follows:
\begin{equation*}
  q =[q_1, q_2, q_3]^T \in
  \left[-30^\circ, 30^\circ \right]
  \times
  \left[-90^\circ, 90^\circ \right]
  \times
  \left[30^\circ, 180^\circ \right]
\end{equation*}

As an additional safety measure, a portion of the resulting workspace (the red coloured area in Figure
\ref{fig:workspace_analysis}) is excluded from operation to prevent collisions with the robot's body or the mounting
structure. A simplified and safe \textbf{Optimal Work Region} is then defined by inscribing a sphere within the
remaining viable workspace depicted in blue. The center of this sphere, $p_0$, is designated as the leg's nominal
\textbf{Rest Position}, which will serve as the origin for gait trajectories.

\subsection{Trajectory Design}

Moving to trajectory generation, the goal is to create a function $p_d$ to define the motion of the foot.
The design of this trajectory is guided by several key principles and assumptions. Firstly, the path
must be parametric, dependent on both the desired walking speed $v$ and the direction of movement $\psi$.
Secondly, the trajectory primitive is generated relative to the leg's central rest position $p_0$, which is
eventually added as a final offset to determine the absolute path $p_d(t)$. For this initial derivation, we
also assume the ground is a flat, predictable plane at a constant height set to 0 (or $p_{z,0}$ after applying
the rest offset).

The gait cycle is composed of two distinct and well defined phases, which needs to be properly stitched together
to ensure smooth ($C^2$) motion. During the \textbf{Stance Phase}, the foot must remain stationary relative to
the ground as the body moves forward. This implies that the foot's velocity relative to the robot's body must
be constant and equal to $-v$ (along the $\psi$ direction). Consequently, the acceleration during this linear
phase is zero. Conversly, during the \textbf{Swing Phase}, the leg should relocate to start a new cycle
while also lifting off the ground.

\subsubsection{Quintic Polynomials}

The simplest and most widely adopted solution in robotics is using fifth-order (quintic) polynomials
\cite{biagiotti2008trajectory, siciliano2009robotics} to move between two points while matching boundary
conditions for position, velocity, and acceleration. A generic quintic polynomial is defined by six
coefficients ($c_0, \dots, c_5$):

$$ p(t) = c_5t^5 + c_4t^4 + c_3t^3 + c_2t^2 + c_1t + c_0 $$

The function $p(t)$ represents the position, while its first and second time derivatives, $v(t)$ and $a(t)$,
represent the velocity and acceleration, respectively:

$$ v(t) = \frac{dp}{dt} = 5c_5t^4 + 4c_4t^3 + 3c_3t^2 + 2c_2t + c_1 $$
$$ a(t) = \frac{d^2p}{dt^2} = 20c_5t^3 + 12c_4t^2 + 6c_3t + 2c_2 $$

To solve for the six unknown coefficients $\mathbf{c} = [c_0, c_1, c_2, c_3, c_4, c_5]^T$, we impose six
known boundary conditions, i.e. the desired position, velocity, and acceleration at the start time ($t = 0$)
and at the end time ($t = T$), where $T$ is the total duration of the movement. Then a system of six linear
equations can be derived and expressed in matrix form as $M \cdot \mathbf{c} = \mathbf{b}$:

$$
  \begin{bmatrix}
    1 & 0 & 0 & 0 & 0 & 0 \\
    0 & 1 & 0 & 0 & 0 & 0 \\
    0 & 0 & 2 & 0 & 0 & 0 \\
    1 & T & T^2 & T^3 & T^4 & T^5 \\
    0 & 1 & 2T & 3T^2 & 4T^3 & 5T^4 \\
    0 & 0 & 2 & 6T & 12T^2 & 20T^3
  \end{bmatrix}
  \begin{bmatrix}
    c_0 \\ c_1 \\ c_2 \\ c_3 \\ c_4 \\ c_5
  \end{bmatrix}
  =
  \begin{bmatrix}
    p_0 \\
    v_0 \\
    a_0 \\
    p_f \\
    v_f \\
    a_f
  \end{bmatrix}
$$

The vector of coefficients $\mathbf{c}$ can then be found by inverting the $6 \times 6$ matrix $M$ and
multiplying it by the vector of boundary conditions $\mathbf{b}$:

\begin{equation}
  \mathbf{c} = M^{-1} \cdot \mathbf{b}
  \label{eqn:quintic_poly_solution}
\end{equation}

The resulting coefficients are constants that depend only on the specified boundary conditions and the total
movement time $T$. The final trajectory $p(t)$ is then a continuous function of the generic time variable
$t \in [0, T]$.

\subsubsection{Horizontal Component}

We start by defining the 1D horizontal component of the trajectory, $p_h(t)$, as a function of normalized time
$t \in [0, 1]$, and representing the motion along the direction of travel $\psi$. The 2D path in the $XY$ plane
is simply this 1D motion projected onto the direction vector $\mathbf{d}(\psi) = [\sin(\psi), \cos(\psi)]^T$.

We define the \textbf{Duty Factor} $\beta$ as the fraction of the cycle spent in the Stance Phase (typically
$\beta > 0.5$ for structural stability, meaning that the robot is supported by at least 3 contact points at every
moment). This divides the normalized unit period into two segments:

$$ T_{stance} = \beta $$
$$ T_{swing} = (1-\beta) $$

The cycle is thus defined with the Swing Phase occurring for $t \in [0, T_{swing}]$ and the Stance Phase for
$t \in [T_{swing}, 1]$. The trajectory oscillates between a forward limit (touchdown) $p_1 = r$ and a backward
limit (liftoff) $p_2 = -r$. The total horizontal stroke is $S = 2r$.

During the Stance Phase, the motion is linear, connecting the touchdown point (at $t = T_{swing}$, $p = r$) to
the liftoff point (at $t = 1$, $p = -r$). The function $p_{h,stance}(t)$ is the equation of this line. Its slope,
the normalized velocity $v_{norm}$ is constant:

$$ v_{norm} = \frac{\Delta p}{\Delta t} = \frac{-2r}{\beta} $$
The trajectory for this phase and its derivatives are given by:
$$ p_{h,stance}(t) = p_1 + v_{norm} \cdot (t - T_{swing}) $$
$$ v_{h,stance}(t) = v_{norm} $$
$$ a_{h,stance}(t) = 0 $$
During the Swing Phase, we use the quintic polynomial method to move from the liftoff position back to the
touchdown position. This function must smoothly connect the end of the previous stance phase (at $t = 1$,
or $t = 0$ in the new cycle) to the start of the current stance phase (at $t = T_{swing}$).

To ensure $C^2$ continuity, we must match the position, velocity, and acceleration of the stance phase at both
ends. We solve for the polynomial $p_{h,swing}(t)$ over the interval $T = T_{swing}$ using the following
boundary conditions vector $\mathbf{b}_{h,swing} = [-r, v_{norm}, 0, r, v_{norm}, 0]^T$.
Solving Equation \ref{eqn:quintic_poly_solution} with this vector yields the specific coefficients for the
horizontal swing polynomial.

\subsubsection{Vertical Component}

Next, we define the vertical component of the motion, $p_z(t)$, relative to the ground plane.

During the stance phase the foot is on the ground providing propulsion, therefore $p_{z,stance}(t) = 0$. This
implies $v_{z,stance} = 0$ and $a_{z,stance}(t) = 0$.

During the swing phase, the leg must lift to a clearance height $H_{lift}$ ($= r$) and return to the ground.
This motion must also be $C^2$ continuous, connecting smoothly to the zero-motion of the Stance Phase. To
achieve this, the Swing Phase is split into two identical halves, "Lift-Up" and "Lift-Down", each with duration
$T_{lift} = T_{swing} / 2$.

We solve for the lift-up polynomial $p_{z,up}(t)$. The boundary conditions must match the stance phase at the
start ($t = 0$) and ensure a smooth apex at the peak ($t = T_{lift}$). The boundary conditions vector is
$\mathbf{b}_{z,up} = [0, 0, 0, H_{lift}, 0, 0]^T$. Then, the lift-down polynomial is a time-mirrored version of
the lift-up segment.

This two-stage approach guarantees $C^2$ continuity for the entire vertical trajectory: it starts from
$p=0, v=0, a=0$ (matching the stance end), achieves a smooth peak at $t = T_{lift}$, and returns to
$p=0, v=0, a=0$ at $t = T_{swing}$ (matching the stance start).

\subsubsection{Path Assembly}

The complete spatial geometry of the gait, $p_{prime}(t)$ is now fully designed, as a function of the
normalized time $t \in [0, 1]$. The complete primitive is assembled by combining the horizontal and vertical
components, projecting the horizontal motion onto the $X$ and $Y$ axes, and stitching the swing and stance
phases together:
$$
p_{prime}(t) =
  \begin{cases}
    \begin{bmatrix}
      p_{h,swing}(t) \sin(\psi) \\
      p_{h,swing}(t) \cos(\psi) \\
      p_{z,swing}(t)
    \end{bmatrix}
    & \text{Swing: } 0 \le t < T_{swing} \\
    \\
    \begin{bmatrix}
      p_{h,stance}(t) \sin(\psi) \\
      p_{h,stance}(t) \cos(\psi) \\
      0
    \end{bmatrix}
    & \text{Stance: } T_{swing} \le t \le 1 \\
  \end{cases}
$$
The desired path $p_d(t)$ sent to the controller is then obtained by biasing this primitive with the
leg's central rest position $p_d(t) = p_0 + p_{prime}(t)$.

Crucially, this formulation decouples the path's spatial geometry from its execution speed.
The function $p_{prime}(t)$ defines only the geometric path, with the input $t$ representing the percentage
of cycle completion, not the actual time.

\subsubsection{Walking Speed Dependance}

The desired physical walking speed $v$ is introduced by controlling how fast this normalized time $t$ advances
in the real world. This is achieved through a discrete-time implementation. First, we determine the required
real-time period ($T_{real}$) for one full gait cycle. The physical stroke $S = 2r$ must be covered at the
desired velocity $v$ during the stance phase, which lasts for a fraction $\beta$ of the total period, therefore
the total real-time period for the cycle is:
$$ T_{real} = \frac{2r}{\beta v} $$
In the control loop, the normalized path $p_{prime}(t)$ is discretized into $n$ samples (e.g. $n = 1000$).
A counter $k$ (where $0 \le k < n$) tracks the current step, and the corresponding normalized time is $t_k = k/n$.
The controller achieves the desired velocity $v$ by incrementing the counter $k$ at a specific real-time
frequency, $f$ determined by the real-time step $\Delta t_{real}$, which is the total period divided by the
number of samples:
$$ \Delta t_{real} = \frac{T_{real}}{n} = \frac{2r}{n \beta v} $$
The controller's update frequency is $f = 1 / \Delta t_{real}$. By adjusting this frequency $f$ (or its inverse,
the time step $\Delta t_{real}$), the desired velocity $v$ is precisely controlled, while the spatial trajectory
remains constant.

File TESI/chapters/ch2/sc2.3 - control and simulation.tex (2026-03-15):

\section{Control and Simulation}
\label{sc:simulation}

Having defined the complete kinematic model via the DH parameters, derived the IK solver, and designed a $C^2$
continuous gait trajectory, we proceed to validate the entire system by simulation. To verify that these
theoretical components function correctly in unison, a digital model of the leg is implemented in the
Simulink \cite{matlab} environment. This simulation serves as a crucial proof-of-concept, allowing for the
verification of the control logic and the workspace before committing to physical hardware. This section details
the open-loop control architecture used for this validation and the construction of the simulation model itself.

\subsection{Open Loop Control Strategy}

The control strategy adopts an open-loop architecture (Figure \ref{fig:control_chain}), deliberately neglecting
external disturbances or modeling errors; its sole purpose is to validate the correctness of the kinematic chain.

It consists in:

\begin{itemize}
  \item \textbf{Path Planning:} The Gait Trajectory Generator outputs the desired Cartesian position $p_d(t)$
    at each time step, given a desired walking speed $v$ and direction $\psi$.
  \item \textbf{Inverse Kinematics:} The desired path $p_d(t)$ is fed into the IK solver, which
    calculates the required vector of joint angles $q_d(t) = [q_1, q_2, q_3]^T$ needed to achieve
    that end-effector position.
  \item \textbf{Leg Model (Plant):} The desired angles $q_d(t)$ are sent as commands to the
    digital twin of the leg, modeled with the aid of the Simscape library.
  \item \textbf{Forward Kinematics:} For validation, the actual joint angles from the simulation model are
    fed into the FK block (based on the DH Table \ref{tab:dh_parameters}). This calculates the resulting
    end-effector position, $p_{sim}(t)$.
\end{itemize}

\begin{figure}[htbp]
    \centering
    
    \caption{Block Diagram of the Open Loop Control Chain.}
    \label{fig:control_chain}
\end{figure}

A key assumption at this stage is the use of ideal actuators. The joints in the simulation are modeled as
ideal position controllers. This means that when a joint is commanded to go to an angle $q_i$, it achieves
this setpoint almost instantaneously and without error. We are intentionally neglecting the dynamics of the
motors (e.g. torque limits, friction, PID control, and settling time) to isolate the validation purely to the
kinematic model.

The goal is to answer the question: "If the joints go to the angles we calculated, does the foot go to the
position we intended?" The simulation is considered successful if the error between the desired path and the
actual path is approximately close to zero for the entire duration.

\subsection{Digital Simulation}

To create a realistic and physically-grounded representation of the leg, the digital twin is constructed using
Simscape Multibody \cite{simscape}. This MATLAB/Simulink toolbox allows for the modeling of 3D mechanical systems
by defining rigid bodies, joints, constraints, and their spatial relationships.

The leg model (reported in Figure \ref{fig:simscape_model}) is built by importing the CAD (Computer-Aided Design)
files for each link (Coxa, Femur, and Tibia) for a better graphical representation. These rigid bodies are then
connected using 'Revolute Joint' and 'Transformation' blocks at the appropriate locations, corresponding to the
physical actuators and established DH parameters. The joint axes and link-to-link coordinate frames are meticulously
aligned ensuring the simulation model is a one-to-one representation of the theoretical kinematic chain.

\begin{figure}[htbp]
    \centering
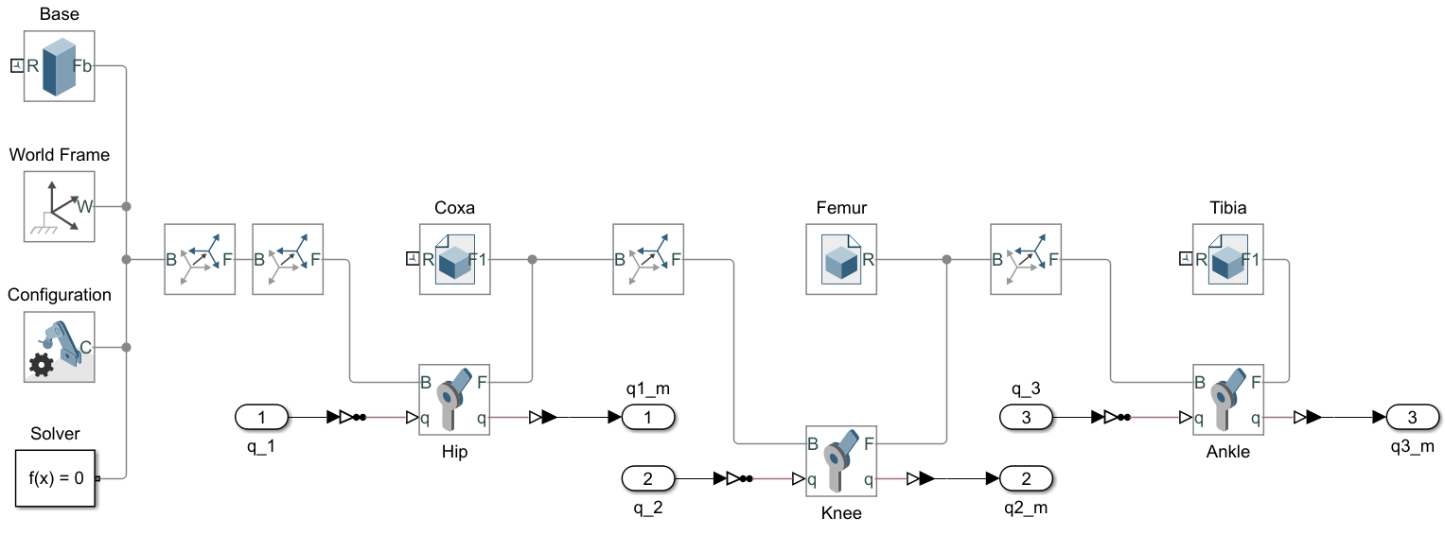
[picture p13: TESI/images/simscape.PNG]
    
    \caption{Simscape Multibody Limb Model (Plant Block).}
    \label{fig:simscape_model}
\end{figure}

This model serves as the 'Plant' block in the control diagram. The inputs to the model are the three desired
joint angles $q_d(t)$ from the IK block, which drive the 'Sensing and Motion' input of the Revolute
Joint blocks. The outputs are the resulting joint angles and poses, which are passed to the FK validation block
and used to generate the 3D animation (as seen in Figure \ref{fig:rendering_side}) for visual confirmation
of the gait.

\begin{figure}[htbp]
    \centering
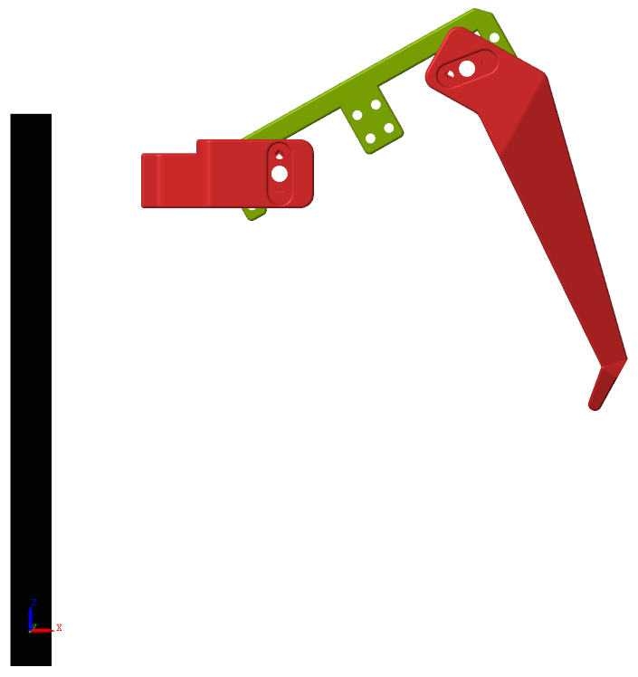
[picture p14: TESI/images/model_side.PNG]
    
    \caption{3D Rendering of the Simscape Simulation (Side View).}
    \label{fig:rendering_side}
\end{figure}

For the purpose of the digital simulation, the walking direction will be set to be coincident with the y axis
($\vec{\psi} = \vec{y}$).

\subsection{Simulation Results}
\label{sec:simulation_results}

The primary validation of the theoretical model comes from a comparison of the desired Cartesian path (the output
of the Path Generator, $p_d$) against the actual path achieved by the Simscape model (the output of the Forward
Kinematics block, $p_{sim}$). These two trajectories (Figure \ref{fig:gait_z_psi}) are undistinguishable,
confirming the entire kinematic chain — from the DH parameters and IK solver to the FK validation — is
mathematically correct and consistent.

\begin{figure}[htbp]
    \centering
    
    \caption{Simulated Gait Ttrajectory in the $Z\psi$-plane (Side View).}
    \label{fig:gait_z_psi}
\end{figure}

The path clearly shows the linear stance phase (where Z is constant) and the smooth, $C^2$ continuous swing
phase, which lifts the foot to the required clearance height. Furthermore, the entire trajectory operates
correctly within the boundaries of the predefined Optimal Workspace Region (OWR).

\subsubsection{Cartesian Space Analysis}

A comprehensive overview of the system's performance in Cartesian space is depicted in Figure \ref{fig:cartesian_results}.

The three plots (X, Y, Z) demonstrate a perfect tracking of the commanded trajectory ($p_d$) as expected from the
ideal actuator assumption. The negligible errors ($e_{sim} \le 0.8\,mm$) are attributed to inertial effects
and a small tracking delay, both reasonable assumptions in real world systems.

\begin{figure}[htbp]
    \centering
    \begin{subfigure}[b]{0.8\textwidth}
        \centering
        
        \caption{Trajectory Tracking}
    \end{subfigure}

    \begin{subfigure}[b]{0.8\textwidth}
        \centering
        
        \caption{Tracking Errors}
    \end{subfigure}
    \caption{Cartesian-Space Simulation Results.}
    \label{fig:cartesian_results}
\end{figure}

\subsubsection{Joint Space Analysis}

Figure \ref{fig:joint_results} confirms that the Cartesian trajectory is correctly translated into smooth,
continuous joint commands, free of any "snaps" or sudden changes even at phase transition points.

Furthermore, all three trajectories operate comfortably within the designated joint limits, confirming the IK
solver is capable of finding a valid and safe solution.

\begin{figure}[htbp]
    \centering
    \begin{subfigure}[b]{0.8\textwidth}
        \centering
        
        \caption{Trajectory Tracking}
    \end{subfigure}

    \begin{subfigure}[b]{0.8\textwidth}
        \centering
        
        \caption{Tracking Errors}
    \end{subfigure}
    \caption{Joint-Space Simulation Results.}
    \label{fig:joint_results}
\end{figure}

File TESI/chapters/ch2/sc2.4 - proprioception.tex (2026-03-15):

\section{Proprioception and Path Adaptation}
\label{sec:proprioception}

The open-loop control strategy and kinematic chain validated in Section 2.2 demonstrated the system's theoretical
correctness under ideal conditions. However, this approach relies on the strict assumption of a perfectly flat
and predictable terrain ($z_{ground} = p_{z,0}$). In a real-world unstructured environment, ground elevation
varies unpredictably. Without feedback, a purely time-driven limb would either strike the ground prematurely
— causing high mechanical stress and potential instability — or fail to reach it entirely, compromising propulsion.

To relax this assumption and enable a "Blind Walking" \cite{brooks1989robot} capability, the system is
augmented with basic proprioceptive sensing and a reactive control layer. Admittedly, while this approach does
not fully solve the locomotion problem for extreme terrain (which would require a more structured control), it
represents the fundamental first step towards robust locomotion: the ability to detect and adapt to the ground
surface upon contact.

\subsection{Contact Sensing and Architectural Shift}

To detect the ground transition, the limb is equipped with a binary contact sensor located at the tip of the
foot. This sensor acts as a logical limit switch, providing a boolean signal $S_c$ to the controller:

$$
  S_c =
  \begin{cases}
    1 & \text{if touching ground}\\
    0 & \text{otherwise}
  \end{cases}
$$

The introduction of this sensor demands a fundamental shift in the control architecture. The path planning
problem transforms from a purely time-dependent function, $p_d(t)$, to a state-dependent system driven by
discrete events.

In the previous open-loop model, the gait phase was dictated by a global clock. In this adaptive model, the
controller must monitor $S_c$ and be capable of interrupting the Swing Phase exactly at the moment of
physical impact. Consequently, the trajectory generator cannot simply map a normalized time $t \in [0,1]$ to a
position; it must be restructured to handle asynchronous events and variable phase durations.

\subsection{Finite State Trajectory Generator}

To implement this reactive logic robustly, a custom Finite State Machine (FSM, Figure \ref{fig:fsm_logic}) was designed
\cite{cruse1990mechanisms}. This generator decouples the logical phase of the leg from the global clock,
allowing for local adaptations while maintaining synchronization through a phase-advance mechanism.

\begin{figure}[htbp]
    \centering
    \begin{tikzpicture}[
        ->,                       % Freccia su tutti i percorsi
        >=Stealth,                % Stile punta freccia moderno
        node distance=3.5cm and 4.5cm, % Distanza verticale e orizzontale
        every state/.style={      % Stile globale per i cerchi degli stati
            draw=black,
            thick,
            fill=gray!10,
            minimum size=3cm,     % Dimensione fissa per cerchi uniformi
            align=center          % Permette "a capo" dentro i cerchi
        },
        thick                     % Linee spesse
    ]

    % --- Definizione degli Stati ---

    % 1. Stance 1 (Alto-Sinistra) - Stato Iniziale
    \node[state, initial left, initial text={Start}] (S1) {Posterior\\Stance\\(Stance 1)};

    % 2. Lift (Alto-Destra) - A destra di S1
    \node[state] (Lift) [right=of S1] {Lift\\(Early Swing)};

    % 3. Touch (Basso-Destra) - Sotto a Lift
    \node[state] (Touch) [below=of Lift] {Touch\\(Late Swing)};

    % 4. Stance 2 (Basso-Sinistra) - A sinistra di Touch (e sotto S1)
    \node[state] (S2) [left=of Touch] {Anterior\\Stance\\(Stance 2)};

    % --- Transizioni (Frecce) ---

    % 1. Stance 1 -> Lift (Freccia verso destra)
    \path (S1) edge node[above, align=center] {
        $p_h \le -r$
    } (Lift);

    % 2. Lift -> Touch (Freccia verso il basso)
    \path (Lift) edge node[right, align=left] {
        $t > T_{lift}$
    } (Touch);

    % 3. Touch -> Stance 2 (Freccia verso sinistra)
    \path (Touch) edge node[below, align=center] {
        $S_c = 1$ \\
        \textit{-- or --} \\
        $t > T_{swing}$
    } (S2);

    % 4. Stance 2 -> Stance 1 (Freccia verso l'alto)
    \path (S2) edge node[left, align=right] {
        $p_h = 0$
    } (S1);

    \end{tikzpicture}
    \caption{Finite State Machine for Adaptive Trajectory Generation.}
    \label{fig:fsm_logic}
\end{figure}

\subsubsection{State 1: Posterior Stance (Stance 1)}

The initial state of the cycle. Geometrically, it corresponds to the leg moving from the central rest
position ($p_h = 0$) towards the posterior limit of the workspace ($p_h = -r$).

\newpage
The horizontal velocity is constant ($\dot{p}_h = -v$). The position is calculated via a discrete-time
integrator, which is reset upon entering the state. The vertical position $z$ is held constant at the
previously detected ground level.

Upon entering this state, the system calculates a synchronization parameter, $\delta(k)$, to compensate for any
timing drift accumulated in the previous cycle $k-1$. Recalling the duty factor $\beta$, the parameter is calculated as:
\begin{equation}
  \delta(k) = \left(1 - \frac{\beta}{2}\right) - t - \delta(k-1)
\end{equation}
where $t$ is the normalized global time counter. This ensures that the leg remains synchronized with the
robot's gait rhythm, correcting for local timing variations.

The system transitions to the Lift state when the horizontal position reaches the posterior stroke limit
($p_h \le -r$).

\subsubsection{State 2: Lift Phase (Early Swing)}

This state represents the deterministic part of the swing phase, where the leg lifts off the ground to clear
potential obstacles.

The duration of this phase, $T_{lift}$, is dynamically calculated to absorb the phase error $\delta(k)$:
\begin{equation}
  T_{lift} = T_{touch} + \delta(k) = \frac{1-\beta}{2} + \delta(k)
\end{equation}
This variable duration is the mechanism that re-synchronizes the leg with the robot's global gait cycle.

A quintic polynomial moves the foot vertically from its current height to the clearance height $H_{lift}$ over
the duration $T_{lift}$, while another quintic polynomial starts repositioning the foot horizontally over the
duration $T_{swing} = T_{lift} + T_{touch}$.

The state transitions only when the timer exceeds the allocated time ($t > T_{lift}$), meaning the foot has
reached the desired clearence height.

\subsubsection{State 3: Touch Phase (Late Swing)}

This state governs the descent of the leg. Crucially, this is where proprioceptive feedback is expected to trigger.

The timer variable is adjusted to parametrize the descent polynomial $t' = t_{norm} - T_{lift}$, guiding the
foot from $H_{lift}$ back towards the nominal ground ($z = 0$) over a fixed duration $T_{touch} = (1-\beta)/2$.
The global timer is maintained to preserve continuity with the swing phase dynamics.

The system exits this state under two distinct conditions:

\begin{enumerate}
  \item \textbf{Time-out:} The time expires ($t' > T_{touch}$ or equivalently $t > T_{swing}$), implying the leg
    completed the full trajectory without contact (e.g. a hole or flat ground).
  \item \textbf{Early Contact:} The sensor triggers ($S_c = 1$). This indicates the ground is higher
    than expected (e.g. an obstacle).
\end{enumerate}

In both cases, the FSM immediately transitions to the next state.

\subsubsection{State 4: Anterior Stance (Stance 2)}

Following the touchdown, the leg enters the anterior portion of the stance phase, moving from the anterior limit
($+r$ or the early contact point) back towards the central rest position ($p_h = 0$).

The horizontal velocity returns to $-v$. The vertical position $z$ is locked at the specific height recorded at
the moment of the Touch $\to$ Anterior Stance transition. This allows the robot to walk "on top" of obstacles rather
than trying to push through them.

The cycle completes when the leg crosses the zero-point of the workspace ($p_h = 0$), triggering the transition
back to Posterior Stance. At this crossing, the cycle index $k$ increments, and the loop repeats.

\subsection{Adaptive Simulation Results}

To validate the proprioceptive controller, the Simscape environment was modified to include an uneven terrain
profile.

Figure \ref{fig:adaptive_results} provides a direct comparison between the nominal, time-based trajectory
and the reactive, adaptive trajectory generated by the FSM in the presence of uneven terrain. For visual
clarity, these plots represent the trajectory primitives defined in the $Z\psi$-plane.

\subsubsection{Vertical Adaptation}

The bottom plot (Vertical Trajectory) clearly demonstrates the effectiveness of the proprioceptive loop. When
the limb encounters a positive obstacle (represented by the gray terrain profile), the adaptive trajectory
deviates from the nominal path exactly at the moment of impact. Unlike the nominal reference, which would
attempt to drive the foot through the terrain, the adaptive system triggers an immediate transition from the Touch
Phase to the Stance Phase. The vertical position is subsequently maintained at the obstacle's height for the
duration of the propulsion stroke, effectively allowing the robot to walk on top of the irregularity rather than
pushing against it.

\begin{figure}[htbp]
    \centering
    
    \caption{Adaptive Gait Simulation with the New FSM Trajectory Generator.}
    \label{fig:adaptive_results}
\end{figure}

\subsubsection{Synchronization and Phase Correction}

Despite the timing disturbances introduced by early ground contacts, the top plot (Horizontal Trajectory) shows
that the system maintains robust synchronization. While the early impact inevitably causes a minor phase lead
(visible as a slight horizontal shift between the purple and green waves), the trajectory does not drift
indefinitely. Instead, when the obstacle is no longer present, the cycle realigns with the non-adaptive ideal
trajectory. This proves that the phase synchronization mechanism successfully compensates for these delays in
subsequent cycles, keeping the limb's rhythm bounded and consistent with the global gait cycle.

\subsubsection{Continuity and Stability Considerations}

There is key consideration to address regarding the kinematic continuity at the impact point: while the
generated trajectory primitives are designed to be $C^2$ continuous, the very nature of the "Blind Walk"
implies that the exact moment of touchdown is unpredictable. Consequently, when the ground is struck earlier
than planned, the vertical velocity changes abruptly from the descent speed to zero (relative to the terrain).
Therefore, at these specific transition points, strict $C^2$ continuity cannot be guaranteed.

Secondly, while effective as a proof of concept, this adaptive generator has specific limitations. For starters,
it currently compensates only for elevated obstacles (protrusions), neglecting potential depressions or holes
in the terrain. Also, unlike the nominal generator, this reactive strategy does not inherently guarantee that
the modified path remains within the Optimal Workspace Region (OWR); without explicit saturation limits, the
adaptation could potentially request kinematically unfeasible positions.

Another important consideration to keep in mind is the dynamic shortening of the foot's contact time introduces
significant stability challenges; therefore, a rigorous balance study is essential for the future implementation
of the full robot.

In summary, this strategy is designed specifically to handle minor terrain irregularities (roughness) rather
than large obstacles, representing a solid foundation for higher level obstacle avoidance planning and control
\cite{saranli2001rhex}.

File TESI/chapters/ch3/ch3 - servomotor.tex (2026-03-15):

\chapter{Custom Smart Actuator Module Design}
\label{ch:servomotor}

The performance of any articulated robotic system is strictly bound by the capabilities of its actuators.
In the context of the hexapod limb designed in Chapter \ref{ch:model}, the requirements for
trajectory tracking accuracy, and smoothness of motion are strict. While the geometric design dictates
the reachable workspace, the actuator dynamic dictates the quality of movement within that space.

To satisfy these requirements without incurring in the prohibitive costs of industrial-grade servomotors
(e.g. Dynamixel-X series \cite{robotis_dynamixel_x}), a custom actuator module was developed, aiming for a good
compromise between performance and cost. This section details the transition from analyzing the limitations of
standard low-cost components to the engineering of a high-performance, "smart" joint module.

\input{chapters/ch3/sc3.1 - limitations.tex}
\input{chapters/ch3/sc3.2 - hardware.tex}
\input{chapters/ch3/sc3.3 - software.tex}
\input{chapters/ch3/sc3.4 - results.tex}

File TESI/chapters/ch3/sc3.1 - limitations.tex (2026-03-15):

\section{Limitations of Commercial Servos}
\label{sec:limitations}

The initial prototyping phase considered the use of the MG996R \cite{mg996r}, a ubiquitous standard-size
servomotor widely adopted in hobbyist robotics. However, a rigorous characterization revealed fundamental
limitations that rendered these units unsuitable for high-fidelity gait control.

The critical deficiencies, ranked by their impact on system performance, are:

\begin{itemize}
    \item \textbf{Feedback Sensor Degradation:} The internal feedback mechanism relies on a low-cost
        resistive potentiometer. Unlike non-contact solutions, this component involves a physical wiper
        sliding over a resistive track. Continuous operation leads to mechanical wear, causing progressive
        signal degradation and non-linearity. This deterioration was experimentally identified as the
        primary source of long-term positioning error.

    \item \textbf{Deadband and Stick-Slip Behavior:} To prevent motor hunting, the MG996R specifies a dead
        band width of $5\,\mu s$~\cite{mg996r}. When combined with the high static friction (stiction) of
        the metal gear assembly, this results in a significant effective dead-zone, making the joint fail
        to move for small command increments.

    \item \textbf{Limited Control Resolution and Bandwidth:} The standard PWM control protocol is inherently
        limited by the update rate. As per specifications, the MG996R operates on a $20\,ms$ period ($50\,Hz$
        frequency)~\cite{mg996r}. This low update frequency acts as a bottleneck for high-dynamic control loops,
        introducing a delay of up to $20\,ms$ between command and actuation.

    \item \textbf{Manufacturing Variability:} Significant unit-to-unit inconsistency was observed regarding
        the operational range characteristics. Two identical servos receiving the same PWM signal often
        align to different physical angles. This lack of repeatability makes the IK model unreliable without
        an intensive, individual calibration for each joint.

    \item \textbf{Obsolete Open-Loop Architecture:} Finally, as confirmed by the standard 3-pin interface
        (PWM, $V_{cc}$, GND)~\cite{mg996r}, these servos operate as "black boxes". The internal PID
        controller is hard-wired and inaccessible, preventing the implementation of advanced friction
        compensation or different control architectures in general. Crucially, the lack of feedback (current,
        real position, temperature) prevents any form of centralized Hardware-in-the-Loop control or online
        diagnostics.
\end{itemize}

To visualize and confirm the newly introduced limitations, an experimental characterization was performed
on two randomly selected units (Motor A and Motor B). The results, presented in Figure
\ref{fig:servo_deficiencies}, map the control signal pulse width ($T_{on}$) against the actual output
angle measured by a high-precision external magnetic encoder. The test involved a full sweep from $0.5\,ms$
to $2.5\,ms$ (Forward path, blue line) followed by a return to $0.5\,ms$ (Backward path, orange line).

\begin{figure}[htbp]
    \centering
    \begin{subfigure}[b]{0.48\textwidth}
        \centering
        
        \caption{}
        \label{fig:motor_A}
    \end{subfigure}
    \hfill
    \begin{subfigure}[b]{0.48\textwidth}
        \centering
        
        \caption{}
        \label{fig:motor_B}
    \end{subfigure}
    \caption{Experimental Characterization of two MG996R Units.}
    \label{fig:servo_deficiencies}
\end{figure}

The dashed black line represents the ideal linear response ($Angle \propto T_{on}$) expected from a servomotor,
adjusted for the motor effective operative range. Both units show severe deviations from this ideal behavior,
introducing position errors exceeding $15^{\circ}$ thus making precise open-loop control impossible without a
complex, motor-specific calibration lookup table.

Furthermore, both plots exhibit a considerable hysteresis loop, visible as the vertical gap between the
forward and backward trajectories for the same PWM input.

Perhaps the most critical finding is the discrepancy between the two nominally identical units. Motor A covers
a range of approximately $0^{\circ}$ to $230^{\circ}$, while Motor B, driven by the exact same signal, spans a
smaller range from roughly $0^{\circ}$ to $200^{\circ}$. It should be noted that the graphs have been truncated
at the endpoints where a change in $T_{on}$ failed to produce any change in output position, indicating
mechanical or electronic saturation.

This inconsistencies confirms that a unified kinematic model cannot be applied to a robot using these actuators.
Each joint would require individual characterization and compensation, which is impractical for scalable
deployment.

Finally, although not visible at this macro-scale zoom, the stepped nature of the data acquisition
(confirmed during testing) revealed that the motors often remained stationary for input changes of
$5-10\,\mu s$ (corresponding to $1-2$ PWM step increments @$50\, Hz$), jumping only when the accumulated
error overcame the internal deadband and static friction.

Given these fundamental constraints, simply upgrading to a slightly more expensive hobby servo would yield
diminishing returns. The only viable solution was to redesign the control electronics entirely, retaining only
the mechanical shell and the DC motor, to create a fully programmable, closed-loop actuator.

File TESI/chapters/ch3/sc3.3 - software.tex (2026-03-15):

\section{Embedded Software Architecture}

The firmware running on the STM32 microcontroller was developed using a modular, object-oriented approach in
C++. This architecture ensures code reusability, encapsulation of hardware specifics, and ease of maintenance
and scalability. The software stack (Appendix \ref{app:software}) is organized into four distinct abstraction
layers, moving from low-level hardware management to high-level application logic.

\subsubsection{Layer 1: Vendor HAL}

The foundational layer consists of the Hardware Abstraction Layer (HAL) provided by the microcontroller
manufacturer. Modules such as \texttt{i2c.h} and \texttt{tim.h} handle the direct register-level configuration
of the MCU peripherals. Relying on these standard verified drivers ensures robust handling of interrupts and
basic I/O operations.

\subsubsection{Layer 2: Custom Middleware and Communication}

This layer acts as a bridge between the raw hardware and the high-level logic, abstracting the communication
protocols. Key modules include:

\begin{itemize}
    \item \textbf{I2C Device Wrappers:} Classes like \texttt{i2c\_device} and \texttt{i2c\_slave} extend the
        Vendor HAL to provide simplified interfaces for bus communication, handling read/write buffers and
        addressing logic.
    \item \textbf{Virtual Register:} This is the core component of the communication architecture. It
        implements the "Virtual Register Map" concept, abstracting the internal state of the actuator
        (positions, gains, modes) as a set of memory-mapped values. This allows the external master to
        interact with the servo seamlessly, as if reading from a standard memory device, changing its
        behaviour dynamically as needed.
\end{itemize}

\subsubsection{Layer 3: High-Level Component Drivers}

This layer contains the specific drivers for the chosen hardware components and the pure algorithmic logic,
independent of the specific MCU.

\begin{itemize}
    \item \textbf{Component Drivers:} The \texttt{AS5600} and \texttt{DRV8870} classes encapsulate the
        specific operational details of the sensor and driver. They utilize the lower layers to perform tasks
        such as reading raw magnetic angles or setting PWM duty cycles, exposing clean methods (e.g.
        \texttt{getAngle()}, \texttt{setSpeed()}) to the application layer.
    \item \textbf{Math and Control:} This module contains the implementation of the control algorithms,
        including the Switching PID logic. It is designed to be purely mathematical, accepting error inputs
        and producing control outputs without direct dependencies on hardware headers.
\end{itemize}

\subsubsection{Layer 4: Application Layer}

The highest level of the hierarchy integrates all previous modules to define the actuator's behavior.

\begin{itemize}
    \item \textbf{Smart Servo Class:} This main class encapsulates the entire logic of the actuator. It
        instantiates the drivers and control modules, managing the data flow between the sensor readings,
        the PID computation, and the motor output.
    \item \textbf{Entry Point:} The \texttt{main.cpp} and \texttt{CONFIG.h} files handle the system
        initialization, configuration, and the execution of the main real-time control loop.
\end{itemize}

\subsection{Control Strategy}

Achieving high-precision positioning in robotic joints is inherently challenging due to the presence of
nonlinear friction phenomena \cite{armstrong1994survey}, specifically static friction (Coulomb) and velocity
weakening effects (Stribeck). As extensively discussed in control literature, standard linear controllers like
the classical PID struggle to manage these non-linearities effectively.

In particular, the integral action required to overcome static friction often leads to overshoot. When
combined with the Stribeck effect, this energy imbalance prevents convergence to the setpoint, resulting in
persistent oscillations known as the "hunting phenomenon". While model-based control techniques could
theoretically compensate for these effects, they require precise parameter identification — which is difficult
to maintain over time due to wear and load changes — and impose a computational burden often incompatible with
low-cost embedded hardware.

A robust alternative that seems to mitigate these issues without requiring complex friction models is the
class of hybrid control strategies, such as Reset or Switching PID \cite{bisoffi2020stick, lorigiola2025switching}.
These approaches modify the internal state of the controller (specifically the integrator) based on discrete
logical rules triggered by the system's state (e.g. zero-crossing of the error or velocity).

The control strategy implemented in this custom actuator is directly derived from the Switching PID strategy
proposed and analyzed in \cite{lorigiola2025switching}. This approach uses a state-machine logic to
dynamically switch the integrator behavior and avoid hunting.

Since the rigorous mathematical derivation and stability proofs of this control strategy are extensive and already
well-documented in the referenced literature, they are considered outside the scope of this thesis. Instead,
this section provides a functional description of the algorithm and the pseudocode implementation specifically
tailored for the custom hardware application.

\subsubsection{Algorithm Description}

\begin{algorithm}[H]
    \footnotesize
    \caption{Switching PID for Friction Compensation}
    \label{alg:switching_pid}
    \begin{algorithmic}[1]
        \Require Reference $r_k$, Measurement $y_k$, Gains $K_p, K_i, K_d$
        \Ensure Control Input $u_k \in [-1, 1]$

        \State $e_k \gets r_k - y_k$ \Comment{Position Error}
        \State $v_k \gets \frac{y_k - y_{k-1}}{\Delta t}$ \Comment{Estimated Velocity}

        \vspace{0.1cm}

        % --- BLOCCO 1: PI Computation (Blu) ---
        \ColorBlock{RoyalBlue}{
            \textbf{1. PI Computation \& Anti-Windup} \\
            $\sigma \gets K_i \cdot e_k$ \\
            $\phi' \gets K_p \cdot (e_k + I_{state})$ \\
            $\phi \gets \text{Saturation of }\phi'$ \\
            $\Delta_{sat} \gets \phi' - \phi$ \\
            \textbf{if} $\text{sgn}(\sigma) == \text{sgn}(\Delta_{sat})$ \textbf{and} $\Delta_{sat} \ne 0$ \textbf{then} \\
            \hspace*{1.5em} $I_{state} \gets I_{state}$ \Comment{Hold integrator} \\
            \textbf{else} \\
            \hspace*{1.5em} $I_{state} \gets I_{state} + \sigma \Delta t$ \Comment{Update integrator} \\
            \textbf{end if}
        }

        \vspace{0.1cm}

        % --- BLOCCO 2: Switching Logic (Arancione) ---
        \ColorBlock{OrangeRed}{
            \textbf{2. Switching Logic} \\
            \textbf{if} $(\text{State} == \textsc{StickSlip}) \textbf{ and } (\sigma \cdot \phi \le 0)$ \textbf{then} \\
            \hspace*{1.5em} $\phi \gets -\phi$ \Comment{Reset energy} \\
            \hspace*{1.5em} $I_{state} \gets \frac{\phi}{K_p} - e_k$ \\
            \hspace*{1.5em} $\text{State} \gets \textsc{Overshoot}$ \\
            \textbf{else if} $(\text{State} == \textsc{Overshoot}) \textbf{ and } (v_k \cdot \phi \ge 0)$ \textbf{then} \\
            \hspace*{1.5em} $\phi \gets K_p \cdot \sigma / K_i$ \Comment{Restore linear behavior} \\
            \hspace*{1.5em} $I_{state} \gets 0$ \\
            \hspace*{1.5em} $\text{State} \gets \textsc{StickSlip}$ \\
            \textbf{end if}
        }

        \vspace{0.1cm}

        % --- BLOCCO 3: Output (Verde) ---
        \ColorBlock{ForestGreen}{
            \textbf{3. Output Calculation} \\
            $u_k \gets \text{Clamp}(\phi - K_d \cdot v_k, -1, 1)$
        }

        \vspace{0.1cm}

        \State \Return $u_k$
    \end{algorithmic}
\end{algorithm}

The control loop runs at a fixed frequency of $1\,\text{kHz}$. At each time step $k$, the algorithm described
in Algorithm \ref{alg:switching_pid} is executed.

The controller operates in two distinct logical states: when in \textbf{Stick-Slip State} (default) the
integrator is fully active to build up the torque necessary to overcome static friction ($F_s$). The logic
prioritizes "breaking out" of the stick phase. Detecting that the error has crossed zero (overshoot) triggers
the transition to the \textbf{Overshoot State}. In this mode, the logic serves to dampen the response by
inverting the control action, preventing the limit cycles (hunting) typical of high-gain PIDs on frictional loads.

The transition between these states is governed by the relationship between the generalized position error
($\sigma$) and the total proportional-integral control effort ($\phi$).

Notably, the term $\phi$ acts as a 'virtual' control effort that is reset discontinuously during state
transitions (Block 2), allowing the controller to instantly adapt its energy based on the
friction regime, a capability not present in standard linear PIDs.

This control strategy is originally derived for set-point regulation (point-to-point motion). While effective for
the quasi-static segments of the gait cycle, its application to dynamic trajectory tracking may require further
tuning or structural modifications (e.g. feed-forward terms). Addressing these specific dynamic tracking
optimization is considered outside the scope of this thesis and is left for future work.

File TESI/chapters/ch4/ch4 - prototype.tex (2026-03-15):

\chapter{Prototype Implementation}
\label{ch:prototype}

Following the successful design and characterization of the custom actuator module, the research progresses
to the system-level integration. This chapter details the physical assembly of the modular robotic limb and
the establishment of the control infrastructure required to bridge the simulation environment with the real
world.

The primary objective of this phase is to validate the mechanical design and the kinematic control strategies
derived in Chapter \ref{ch:model} under real-world conditions. The validation relies on a
Hardware-in-the-Loop (HIL) architecture, which allows for direct comparison between the theoretical model
and the physical prototype.

The scope of these experiments is strictly limited to the verification of the kinematic model and trajectory tracking
capabilities in an open-loop configuration. The proprioceptive and adaptive control strategies discussed in Section
\ref{sec:proprioception}, while validated in simulation, are excluded from this experimental verification due to
project time constraints.

\input{chapters/ch4/sc4.1 - assembly.tex}
\input{chapters/ch4/sc4.2 - performance.tex}

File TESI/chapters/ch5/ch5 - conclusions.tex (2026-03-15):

\chapter{Conclusions}
\label{ch:conclusions}

This thesis has documented the complete engineering cycle of a modular robotic limb, moving from the theoretical
kinematic analysis to the physical realization of a high-performance, cost-effective actuation system. The central
challenge addressed in this work was the "actuation bottleneck" typical of low-cost robotics, where the mechanical
and control performance is severely limited by the poor quality of commercial hobbyist servo-motors. By adopting a
top-down design methodology, supported by simulation and component-level redesign, this research successfully
demonstrated that high-fidelity control can be achieved without resorting to prohibitively expensive industrial
hardware.

\section{Achievements and Considerations}

The primary technical achievement of this work is the development and validation of the custom "Smart Actuator" module.
The transition from a standard analog architecture to a fully digital, microcontroller-based system yielded quantifiable
improvements in every key performance metric.

As demonstrated by the experimental benchmarking in Chapter \ref{ch:servomotor}, the custom module reduced the Root
Mean Square Error (RMSE) in position tracking from an average of $\approx 14^{\circ}$ (observed in the original MG996R
units) to just $0.37^{\circ}$. This result confirms that the limitations of low-cost robotics are often not mechanical
but electronic and algorithmic. Specifically:
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

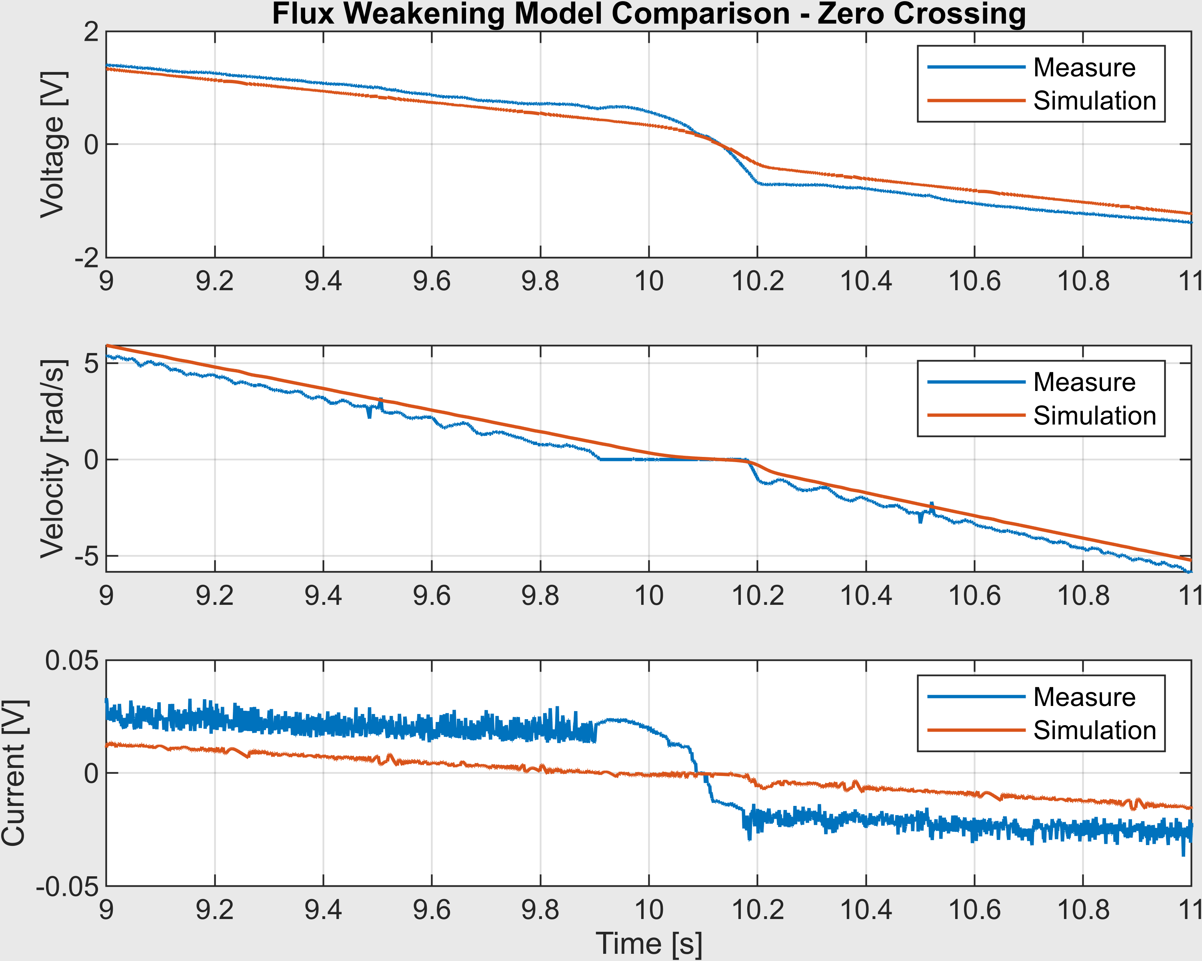
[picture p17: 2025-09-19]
MATLAB/Figures/flux_comparison_zoom.png

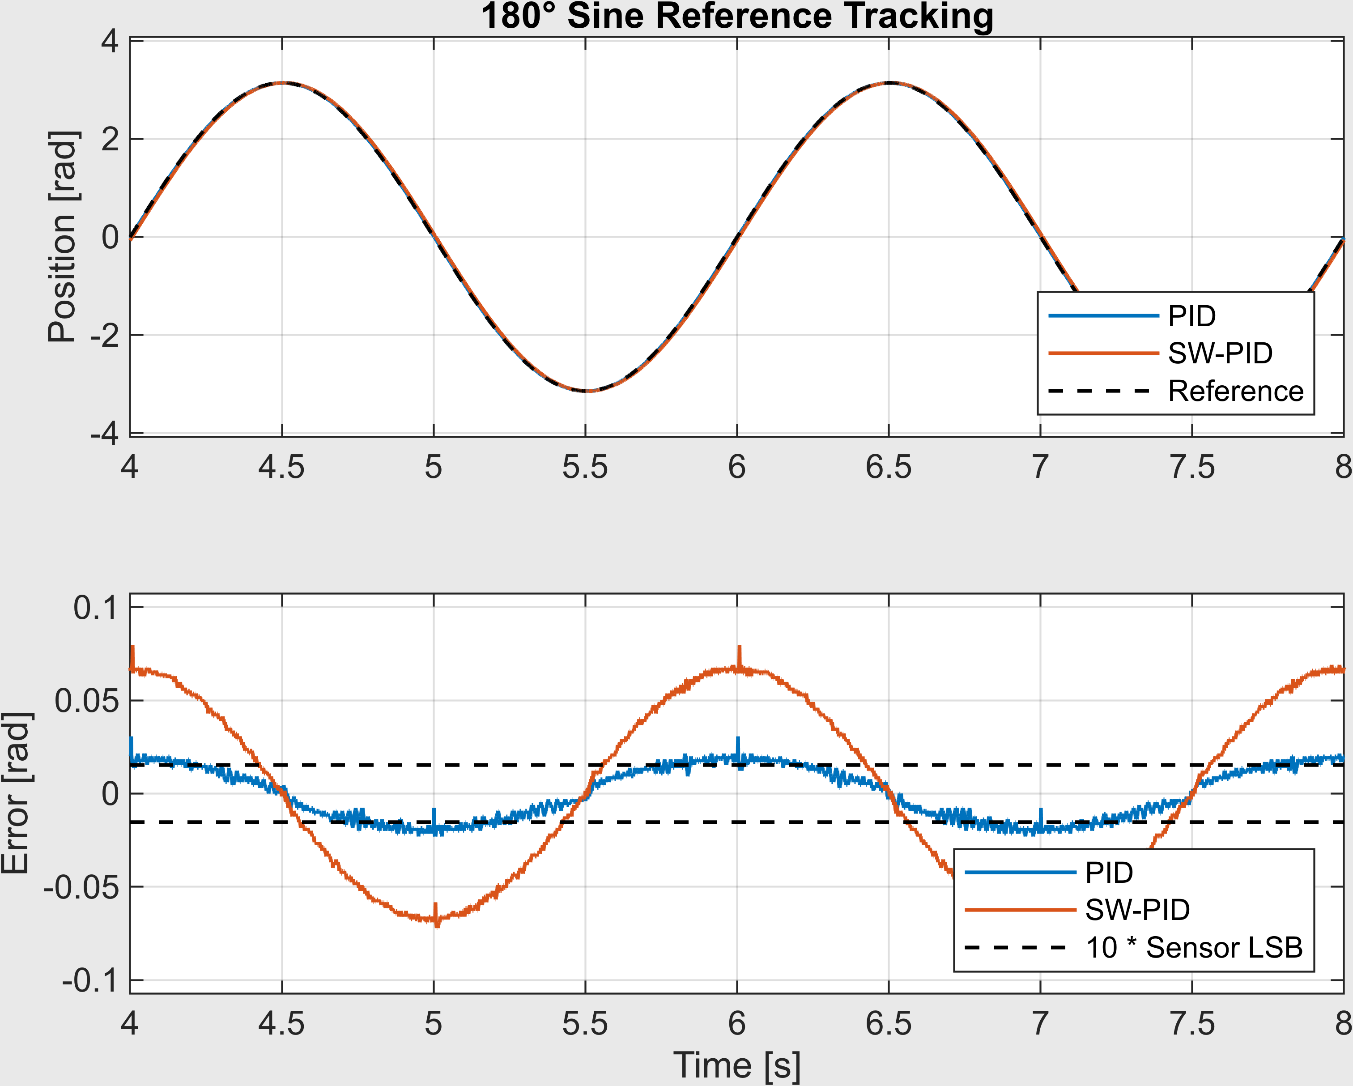
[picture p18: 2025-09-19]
MATLAB/Figures/controller_comparison_tracking.png

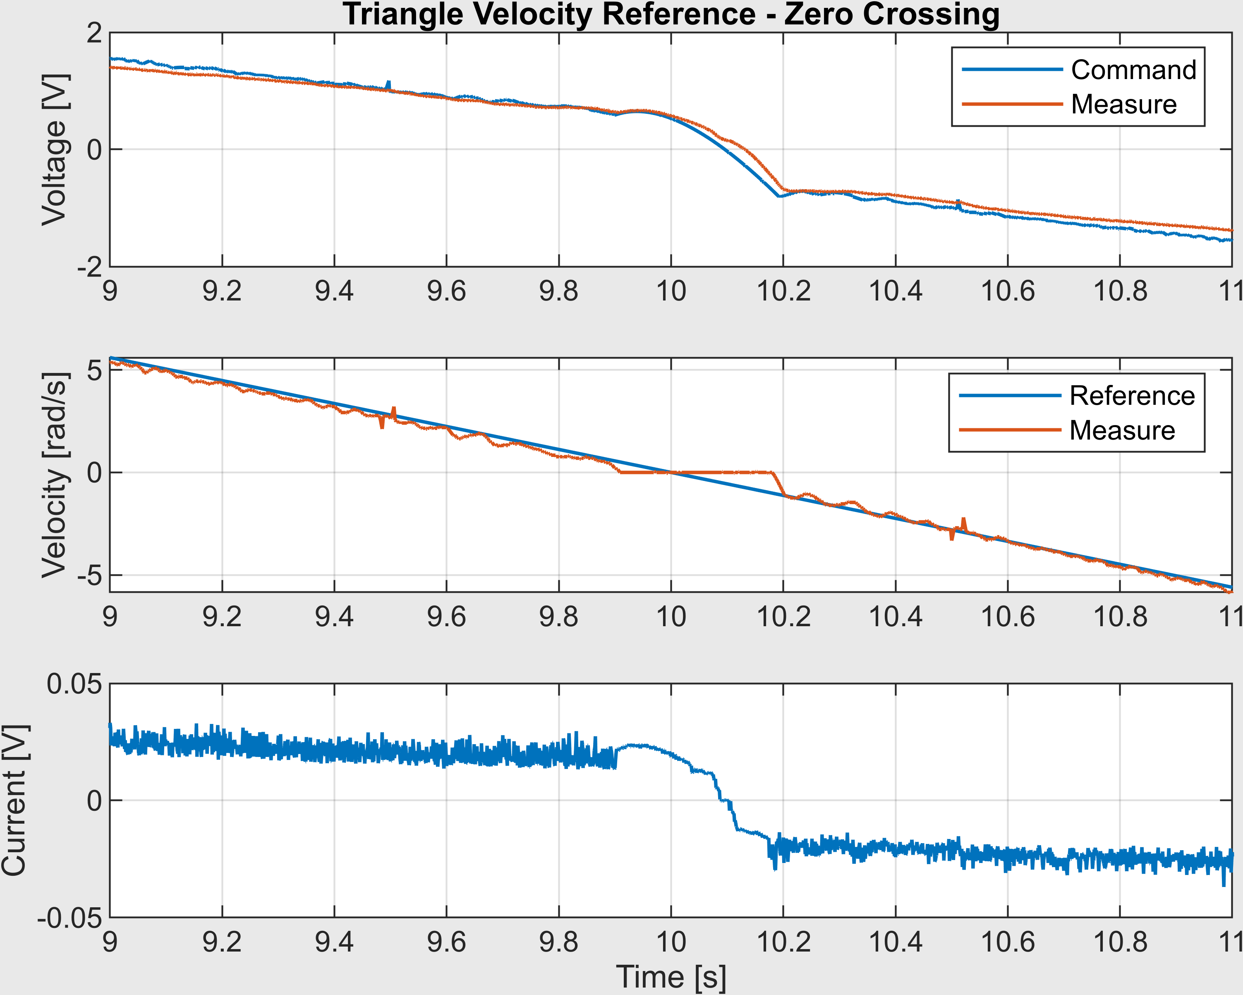
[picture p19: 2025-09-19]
MATLAB/Figures/velocity_triangle_zoom.png

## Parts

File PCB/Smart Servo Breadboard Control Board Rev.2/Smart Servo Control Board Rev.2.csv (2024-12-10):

Source: | D:\Data\_PROGETTI\PRJ_SMART_SERVO\PCB\Smart Servo Control Board Rev.1\Smart Servo Control Board Rev.1.kicad_sch
Date: | 06/12/2023 01:29:35
Tool: | Eeschema (6.0.0)
Generator: | D:\Programs\KiCad\6.0\bin\scripting\plugins/bom_csv_grouped_by_value.py
Component Count: | 38
Individual Components:
Item | Qty | Reference(s) | Value | LibPart | Footprint | Datasheet
 |  | C1 | 10uF | Device:C_Polarized | Capacitor_SMD:C_0603_1608Metric_Pad1.08x0.95mm_HandSolder | ~
 |  | C2 | 100nF | Device:C | Capacitor_SMD:C_0603_1608Metric_Pad1.08x0.95mm_HandSolder | ~
 |  | C3 | 100nF | Device:C | Capacitor_SMD:C_0603_1608Metric_Pad1.08x0.95mm_HandSolder | ~
 |  | C4 | 100nF | Device:C | Capacitor_SMD:C_0603_1608Metric_Pad1.08x0.95mm_HandSolder | ~
 |  | C5 | 100nF | Device:C | Capacitor_SMD:C_0603_1608Metric_Pad1.08x0.95mm_HandSolder | ~
 |  | C6 | 100nF | Device:C | Capacitor_SMD:C_0603_1608Metric_Pad1.08x0.95mm_HandSolder | ~
 |  | C7 | 100nF | Device:C | Capacitor_SMD:C_0603_1608Metric_Pad1.08x0.95mm_HandSolder | ~
 |  | C8 | 10uF | Device:C_Polarized | Capacitor_SMD:C_0603_1608Metric_Pad1.08x0.95mm_HandSolder | ~
 |  | C9 | 100nF | Device:C | Capacitor_SMD:C_0603_1608Metric_Pad1.08x0.95mm_HandSolder | ~
 |  | C10 | 100nF | Device:C | Capacitor_SMD:C_0603_1608Metric_Pad1.08x0.95mm_HandSolder | ~
 |  | C11 | 100nF | Device:C | Capacitor_SMD:C_0603_1608Metric_Pad1.08x0.95mm_HandSolder | ~
 |  | C12 | 100nF | Device:C | Capacitor_SMD:C_0603_1608Metric_Pad1.08x0.95mm_HandSolder | ~
 |  | C13 | 100nF | Device:C | Capacitor_SMD:C_0603_1608Metric_Pad1.08x0.95mm_HandSolder | ~
 |  | C14 | 100nF | Device:C | Capacitor_SMD:C_0603_1608Metric_Pad1.08x0.95mm_HandSolder | ~
 |  | J1 | PRGR | Connector:Conn_01x04_Female | Connector_PinSocket_2.54mm:PinSocket_1x04_P2.54mm_Vertical | ~
 |  | J2 | CTRL | Connector:Conn_01x04_Female | Connector_PinSocket_2.54mm:PinSocket_1x04_P2.54mm_Vertical | ~
 |  | J3 | CTRL | Connector:Conn_01x04_Female | Connector_PinSocket_2.54mm:PinSocket_1x04_P2.54mm_Vertical | ~
 |  | J4 | MOT | Connector:Conn_01x01_Female | Connector_PinSocket_2.54mm:PinSocket_1x01_P2.54mm_Vertical | ~
 |  | J5 | MOT | Connector:Conn_01x01_Female | Connector_PinSocket_2.54mm:PinSocket_1x01_P2.54mm_Vertical | ~
 |  | Q1 | AO3400A | Transistor_FET:AO3400A | Package_TO_SOT_SMD:SOT-23 | http://www.aosmd.com/pdfs/datasheet/AO3400A.pdf
 |  | Q2 | AO3400A | Transistor_FET:AO3400A | Package_TO_SOT_SMD:SOT-23 | http://www.aosmd.com/pdfs/datasheet/AO3400A.pdf
 |  | R1 | 100R | Device:R | Resistor_SMD:R_0603_1608Metric_Pad0.98x0.95mm_HandSolder | ~
 |  | R2 | 10K | Device:R | Resistor_SMD:R_0603_1608Metric_Pad0.98x0.95mm_HandSolder | ~
 |  | R3 | 10K | Device:R | Resistor_SMD:R_0603_1608Metric_Pad0.98x0.95mm_HandSolder | ~
 |  | R4 | 100m | Device:R | Resistor_SMD:R_1206_3216Metric_Pad1.30x1.75mm_HandSolder | ~
 |  | R5 | 100m | Device:R | Resistor_SMD:R_1206_3216Metric_Pad1.30x1.75mm_HandSolder | ~
 |  | R6 | 10K | Device:R | Resistor_SMD:R_0603_1608Metric_Pad0.98x0.95mm_HandSolder | ~
 |  | R7 | 10K | Device:R | Resistor_SMD:R_0603_1608Metric_Pad0.98x0.95mm_HandSolder | ~
 |  | R8 | 100R | Device:R | Resistor_SMD:R_0603_1608Metric_Pad0.98x0.95mm_HandSolder | ~
 |  | R9 | 10K | Device:R | Resistor_SMD:R_0603_1608Metric_Pad0.98x0.95mm_HandSolder | ~
 |  | R10 | 10K | Device:R | Resistor_SMD:R_0603_1608Metric_Pad0.98x0.95mm_HandSolder | ~
 |  | U1 | AMS1117-3.3 | Regulator_Linear:AMS1117-3.3 | Package_TO_SOT_SMD:SOT-223-3_TabPin2 | http://www.advanced-monolithic.com/pdf/ds1117.pdf
 |  | U2 | STM32F030C8Tx | MCU_ST_STM32F0:STM32F030C8Tx | Package_QFP:LQFP-48_7x7mm_P0.5mm | http://www.st.com/st-web-ui/static/active/en/resource/technical/document/datasheet/DM00088500.pdf
 |  | U3 | INA219AxD | Analog_ADC:INA219AxD | Package_SO:SOIC-8_3.9x4.9mm_P1.27mm | http://www.ti.com/lit/ds/symlink/ina219.pdf
 |  | U4 | INA219AxD | Analog_ADC:INA219AxD | Package_SO:SOIC-8_3.9x4.9mm_P1.27mm | http://www.ti.com/lit/ds/symlink/ina219.pdf
 |  | U5 | IRF7307 | :IRF7307_2 | Package_SO:SOIC-8_3.9x4.9mm_P1.27mm
 |  | U6 | AS5600 | Custom:AS5600 | Package_SO:SOIC-8_3.9x4.9mm_P1.27mm
 |  | U7 | IRF7307 | Custom:IRF7307 | Package_SO:SOIC-8_3.9x4.9mm_P1.27mm
Collated Components:
Item | Qty | Reference(s) | Value | LibPart | Footprint | Datasheet
1 | 2 | C1, C8 | 10uF | Device:C_Polarized | Capacitor_SMD:C_0603_1608Metric_Pad1.08x0.95mm_HandSolder | ~
2 | 12 | C2, C3, C4, C5, C6, C7, C9, C10, C11, C12, C13, C14 | 100nF | Device:C | Capacitor_SMD:C_0603_1608Metric_Pad1.08x0.95mm_HandSolder | ~
3 | 1 | J1 | PRGR | Connector:Conn_01x04_Female | Connector_PinSocket_2.54mm:PinSocket_1x04_P2.54mm_Vertical | ~
4 | 2 | J2, J3 | CTRL | Connector:Conn_01x04_Female | Connector_PinSocket_2.54mm:PinSocket_1x04_P2.54mm_Vertical | ~
5 | 2 | J4, J5 | MOT | Connector:Conn_01x01_Female | Connector_PinSocket_2.54mm:PinSocket_1x01_P2.54mm_Vertical | ~
6 | 2 | Q1, Q2 | AO3400A | Transistor_FET:AO3400A | Package_TO_SOT_SMD:SOT-23 | http://www.aosmd.com/pdfs/datasheet/AO3400A.pdf
7 | 2 | R1, R8 | 100R | Device:R | Resistor_SMD:R_0603_1608Metric_Pad0.98x0.95mm_HandSolder | ~
8 | 6 | R2, R3, R6, R7, R9, R10 | 10K | Device:R | Resistor_SMD:R_0603_1608Metric_Pad0.98x0.95mm_HandSolder | ~
9 | 2 | R4, R5 | 100m | Device:R | Resistor_SMD:R_1206_3216Metric_Pad1.30x1.75mm_HandSolder | ~
10 | 1 | U1 | AMS1117-3.3 | Regulator_Linear:AMS1117-3.3 | Package_TO_SOT_SMD:SOT-223-3_TabPin2 | http://www.advanced-monolithic.com/pdf/ds1117.pdf
11 | 1 | U2 | STM32F030C8Tx | MCU_ST_STM32F0:STM32F030C8Tx | Package_QFP:LQFP-48_7x7mm_P0.5mm | http://www.st.com/st-web-ui/static/active/en/resource/technical/document/datasheet/DM00088500.pdf
12 | 2 | U3, U4 | INA219AxD | Analog_ADC:INA219AxD | Package_SO:SOIC-8_3.9x4.9mm_P1.27mm | http://www.ti.com/lit/ds/symlink/ina219.pdf
13 | 1 | U5 | IRF7307 | :IRF7307_2 | Package_SO:SOIC-8_3.9x4.9mm_P1.27mm
14 | 1 | U6 | AS5600 | Custom:AS5600 | Package_SO:SOIC-8_3.9x4.9mm_P1.27mm
15 | 1 | U7 | IRF7307 | Custom:IRF7307 | Package_SO:SOIC-8_3.9x4.9mm_P1.27mm

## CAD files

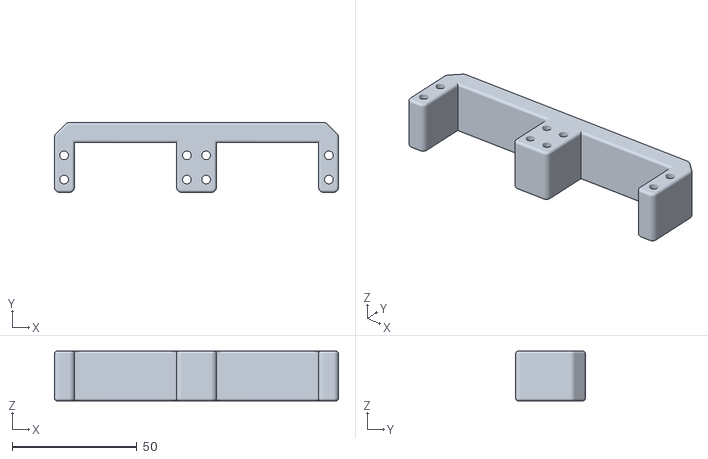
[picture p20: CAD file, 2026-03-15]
MATLAB/Arm Simulation/3D Models/femur.stl
114.0 x 28.0 x 20.0

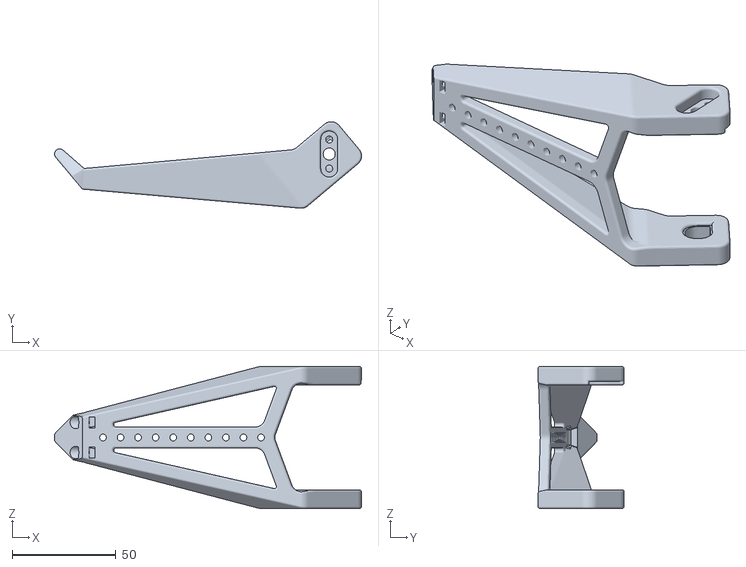
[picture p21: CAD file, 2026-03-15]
MATLAB/Arm Simulation/3D Models/tibia.stl
148.1 x 41.7 x 68.5

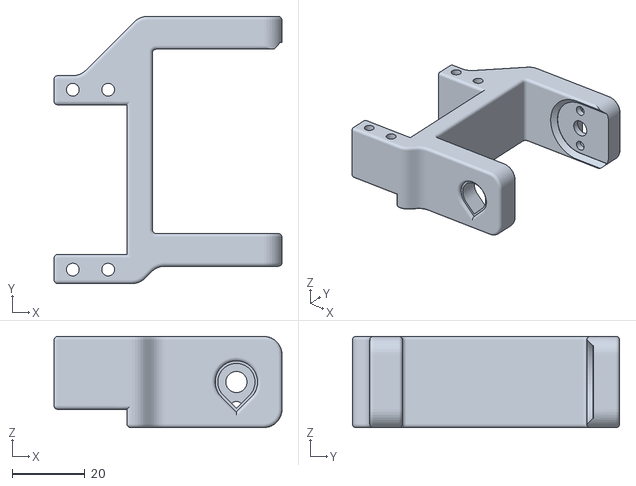
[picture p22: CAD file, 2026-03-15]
MATLAB/Arm Simulation/3D Models/coxa.stl
62.5 x 73.2 x 25.0

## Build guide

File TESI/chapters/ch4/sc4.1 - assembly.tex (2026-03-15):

\section{Hardware-in-the-Loop Architecture}

The successful implementation of the prototype relies on the seamless integration of the mechanical hardware
with the control software. To bridge the theoretical environment (MATLAB/Simulink) with the physical reality, a
Hardware-in-the-Loop (HIL) architecture was established. This approach allows the complex kinematic algorithms
to run on the host PC, while a dedicated embedded bridge manages the low-level communication with the distributed
actuator network.

\subsubsection{Physical Assembly}

The mechanical structure of the limb was realized through additive manufacturing (3D printing) using the CAD
models developed during the design phase. The structural links (Coxa, Femur, Tibia) were printed in PLA to
ensure an optimal stiffness-to-weight ratio.

These components were assembled with the three newly designed custom actuator modules described in Chapter
\ref{ch:servomotor} (see Figure \ref{fig:limb_assembly}). A critical design feature introduced in this assembly is
the axis extension mechanism. To mitigate the radial stress on the servo output shaft an idler bearing was integrated
into the frame opposite to the motor shaft. This configuration effectively creates a simply supported beam structure,
significantly increasing mechanical stability.

\begin{figure}[htbp]
    \centering
    
    \caption{Mechanical Assembly of the Prototype Limb.}
    \label{fig:limb_assembly}
\end{figure}

With the exception of the custom actuator housings and fasteners, the physical limb geometrically coincides perfectly
with the numerical model used in the simulations (Section \ref{sc:simulation}), providing a first visual
confirmation of the prototype's fidelity.

\subsubsection{Simulink/Arduino Control Environment}

The Simulink model, originally developed for pure digital simulation, acts as the High-Level Controller. The
"Leg Model (Plant)" block used in Chapter \ref{ch:model} is replaced by a Serial Interface Block. This modified
control scheme (Figure \ref{fig:hil_scheme}) operates as follows:

\begin{enumerate}
    \item Generation and Transmission: The Path Planner and Inverse Kinematics blocks generate the reference
        joint angles $q_d$ in real-time. These references are quantized and transmitted via USB-Serial to the
        microcontroller bridge.
    \item Hardware Bridge: The interface between the host PC and the actuator network is managed by an Arduino
        board (Arduino Mega 2560). The firmware sketch, parses the UART data and forwards the position setpoints
        to the actuator network via $\text{I}^2\text{C}$ bus. Immediately after it queries their current position
        (also via $\text{I}^2\text{C}$). Then the received data ($q_{hw}$) is transmitted back to Simulink.
    \item Feedback Loop: After the return packet containing the measured joint angles $q_{hw}$ arrives, the
        feedback data is fed into the Forward Kinematics block to reconstruct the actual end-effector position
        $p_{hw}$ for performance analysis.
\end{enumerate}

\begin{figure}[htbp]
    \centering
    
    \caption{Block Diagram of the Hardware-in-the-Loop Control Architecture.}
    \label{fig:hil_scheme}
\end{figure}

\subsubsection{Experimental Protocol}

To ensure a rigorous validation, the experimental setup is designed to strictly mirror the conditions of the
digital simulation presented in Chapter \ref{ch:model}. The reference input for the physical limb is the exact
same $C^2$ continuous gait trajectory derived in Section \ref{sec:trajectory}.

The real-time control chain operates at a fixed update frequency of $100\,\text{Hz}$ ($\Delta t = 10\,\text{ms}$).
In each cycle, the Simulink High-Level Controller samples the continuous trajectory, computes the inverse
kinematics solution $q_d$, and transmits the packet to the embedded bridge. Synchronously, the actual joint
positions $q_{hw}$ are acquired from the actuators and logged.

The primary objective of this experiment is to quantify the \textit{Sim-to-Real} gap by overlaying the
experimental data on the simulation results.

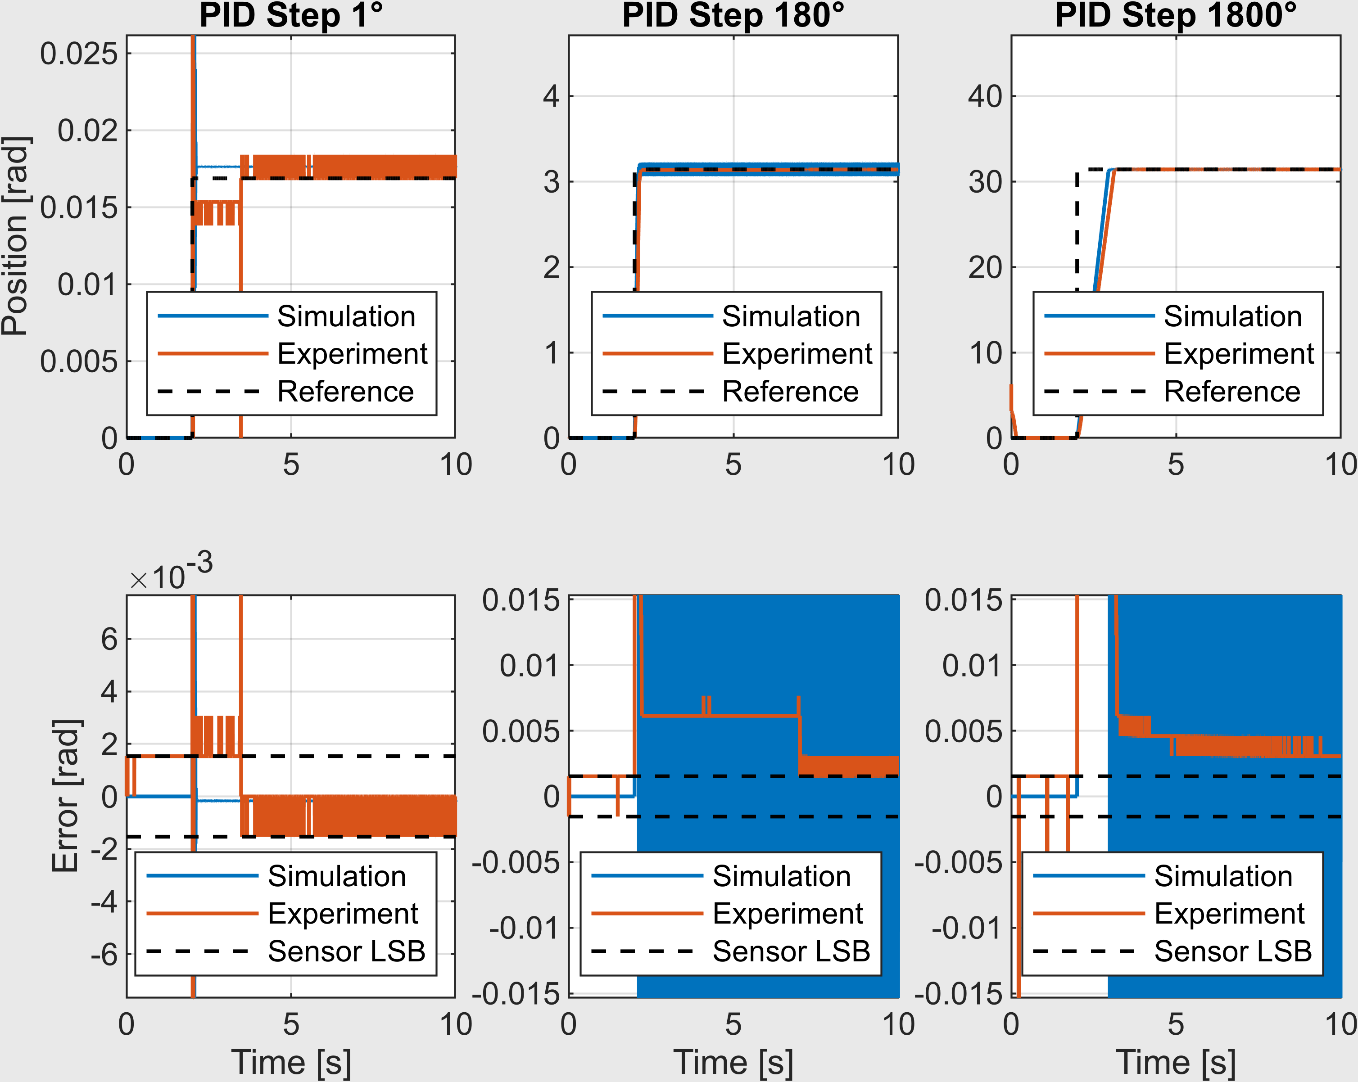
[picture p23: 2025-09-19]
MATLAB/Figures/PID_steps.png

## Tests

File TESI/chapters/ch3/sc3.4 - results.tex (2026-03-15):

\section{Module Characterization and Benchmarking}

The mechanical design and control strategy were validated by subjecting the custom actuator module to an
experimental characterization mirroring the one applied to to the commercial units in Section
\ref{sec:limitations} The tests were conducted using the integrated AS5600 magnetic sensor for feedback,
with the module powered at a nominal voltage of $6.7\,\text{V}$. The $\text{I}^2\text{C}$ bus was used to
transmit the target position directly as a 12-bit digital setpoint, bypassing the resolution limits of
standard PWM signaling.

\subsection{Static Analysis: Linearity and Hysteresis}

The first validation step focused on the static input-output relationship. A slow triangular ramp reference
($100\,ms$ per sensor LSB) spanning the full range in both Forward and Backward directions was administered
to the module. Figure \ref{fig:custom_linearity} illustrates the experimental results.

Compared to the commercial servo baseline (refer to Figure \ref{fig:servo_deficiencies}), the custom module
demonstrates significant visible improvements:

\begin{itemize}
    \item \textbf{Linearity:} The response closely follows the ideal characteristic $y=x$. The distortion,
        typical of the potentiometer-based commercial unit, is effectively eliminated.
    \item \textbf{Hysteresis Suppression:} The forward and backward paths are virtually indistinguishable at
        full scale. The removal of the mechanical potentiometer in favor of the non-contact magnetic sensor
        drastically reduces mechanical backlash, ensuring high repeatability regardless of the direction of
        approach.
    \item \textbf{Range Extension:} The operating range is no longer constrained by the physical limits of
        the potentiometer, granting access to the full $360^\circ$ of rotation. This continuous capability
        necessitates software phase unwrapping to ensure seamless transitions across the zero-crossing point.
\end{itemize}

\begin{figure}[htbp]
    \centering
    \begin{subfigure}[c]{0.48\textwidth}
        \centering
        
        \caption{Full-scale linearity analysis.}
        \label{fig:custom_linearity_full}
    \end{subfigure}
    \hfill
    \begin{subfigure}[c]{0.48\textwidth}
        \centering
        
        \caption{Zoomed view showing micro-linearity.}
        \label{fig:custom_linearity_zoom}
    \end{subfigure}
    \caption{Input-Output Characteristic of the Custom Actuator.}
    \label{fig:custom_linearity}
\end{figure}

\subsection{Step Response Analysis: Sensitivity and Settling}

The module was then subjected to a series of step commands (square waves) of varying amplitudes: Micro-step
($1^\circ$), Mid-range ($15^\circ$), and Full-scale ($90^\circ$).

The results, presented in Figure \ref{fig:step_responses} and \ref{fig:step_error}, highlight two key behaviors:

\begin{itemize}
    \item \textbf{Resolution and Sensitivity ($1^\circ$):} Unlike the commercial unit, which exhibited a
        significant deadband preventing fine adjustments, the custom module responds reliably to micro-step
        commands as small as $1^\circ$ ($\approx 11$ LSB). Note that the visible jitter at this stage is sensor
        noise.
    \item \textbf{Transient Response ($15^\circ, 90^\circ$):} For larger transitions, the motor reaches the
        target setpoint rapidly. While a slight overshoot is visible, the system settles quickly without
        entering a limit cycle (hunting), validating the effectiveness of the Switching PID control algorithm.
\end{itemize}

\begin{figure}[htbp]
\centering
    
    \caption{Trajectory Tracking}
    \label{fig:step_responses}
\end{figure}

\begin{figure}[htbp]
    \centering
    
    \caption{Tracking Errors}
    \label{fig:step_error}
\end{figure}

\subsection{Results Summary}

The experimental results confirm that the custom actuator meets the strict requirements of the limb
application. The redesign has yielded a substantial increase in precision, accuracy, and controllability.
The transition to a digital interface ensures scalability and flexibility, while the mechanical form factor
remains compatible with the original design.

To quantify these improvements, a direct benchmark comparison was performed against the two commercial units
characterized in Section \ref{sec:limitations}. Figure \ref{fig:benchmark} illustrates the performance metrics
regarding positioning accuracy and mechanical play.

For the sake of brevity, the mathematical definitions of the metrics used in this analysis (RMSE, Absolute
Error, Hysteresis) are detailed in Appendix \ref{app:metrics}.

\begin{figure}[htbp]
    \centering
    
    \caption{Performance Benchmark Results.}
    \label{fig:benchmark}
\end{figure}

The data reveals a dramatic enhancement in performance:

\begin{itemize}
    \item \textbf{Accuracy:} The Root Mean Square Error (RMSE), which serves as a reliable indicator of
        global linearity and tracking fidelity, dropped from an average of $\approx 14^{\circ}$ in the
        commercial units to just $\mathbf{0.37^{\circ}}$ in the custom prototype. This result comfortably
        satisfies the design requirement of $<\pm 0.5^{\circ}$ set in Section \ref{sec:hardware}.
    \item \textbf{Peak Error:} The Maximum Absolute Error was reduced from extreme values
        ($\approx 29^{\circ}$ for Unit A) to a manageable $\mathbf{1.49^{\circ}}$, effectively eliminating
        the macroscopic non-linearities observed in the analog potentiometers.
    \item \textbf{Hysteresis:} The stick-slip and backlash effects were significantly mitigated. The average
        hysteresis was reduced from $\approx 5^{\circ}$ to $\mathbf{0.65^{\circ}}$, validating the
        effectiveness of the Switching PID strategy in compensating for static friction.
\end{itemize}

Finally, a cost analysis (Appendix \ref{app:bom}) indicates that these performance gains were achieved within
a very limited budget, proving the viability of the proposed custom solution over expensive high-end commercial
alternatives. Further hardware and software improvements can be implemented in the next revision and are left
as future work.

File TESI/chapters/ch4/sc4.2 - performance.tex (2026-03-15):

\section{Performance Assessment and Results}

The following results provide a quantitative comparison between the reference command ($p_d$, $q_d$), the
simulated response ($p_{sim}$, $q_{sim}$), and the actual experimental telemetry ($p_{hw}$, $q_{hw}$).

\subsubsection{Cartesian Trajectory Tracking}

Figure \ref{fig:gait_z_psi_exp} illustrates the side-view trajectory ($Z\psi$-plane) of the end-effector. Visual
inspection confirms that the physical limb successfully replicates the desired gait profile. The stance phase remains
reasonably flat, while the swing phase achieves the target clearance height without significant deviation. Crucially,
the experimental path (orange) remains close to the Optimal Workspace Region (dotted line), validating the
safety margins established during the design phase.

\begin{figure}[htbp]
    \centering
    
    \caption{Experimental Gait Trajectory in the $Z\psi$-plane (Side View).}
    \label{fig:gait_z_psi_exp}
\end{figure}

Figure \ref{fig:gait_spacetime} shows the time evolution of the trajectory in a 3D graph. Several persistent
perturbations can be seen along the path. This is attributed to model calculation lags on the simulink side,
as they appear during the FSM path generator state transition, and also to external force (gravity).

\begin{figure}[htbp]
    \centering
    
    \caption{Experimental Gait Trajectory in Space-Time.}
    \label{fig:gait_spacetime}
\end{figure}

A time-domain analysis of the Cartesian coordinates is provided in Figure \ref{fig:cart_traj_exp}. The experimental
tracking shows a high degree of fidelity, with all the coordinates closely following the command. The $X$ coordinate,
which should ideally remain constant, shows minor fluctuations ($< 2$ mm) negligible for locomotion stability, while
the $Y$ (propulsion) and $Z$ (lift) components exhibit a small tracking delay. This is expected due to the discrete
nature of the control loop.

\begin{figure}[htbp]
    \centering
    \begin{subfigure}[b]{0.8\textwidth}
        \centering
        
        \caption{Trajectory Tracking}
        \label{fig:cart_traj_exp}
    \end{subfigure}

    \begin{subfigure}[b]{0.8\textwidth}
        \centering
        
        \caption{Tracking Errors}
        \label{fig:cart_err_exp}
    \end{subfigure}
    \caption{Cartesian-Space Experiment Results.}
    \label{fig:cart_exp}
\end{figure}

The error plot (Figure \ref{fig:cart_err_exp}) reveals similarities in the simulation and experimental error shapes,
fundamentally changing only in amplitude (refer also to Figure \ref{fig:joint_results} for better understanding).
The amplitude difference can be attributed to a higher tracking delay, while the shape of the error is reasonably
due to inertial effects, purposely neglected at this stage of control.

\subsubsection{Joint Space Performance}

The performance at the actuator level is detailed in Figures \ref{fig:joint_traj_exp} and \ref{fig:joint_err_exp},
where once again it is visible how all three joints ($q_1, q_2, q_3$) track their respective references with
remarkable precision (also in this instance, the Simulation and Experimental plots differ by amplitude rather than
shape).

\begin{figure}[htbp]
    \centering
    \begin{subfigure}[b]{0.8\textwidth}
        \centering
        
        \caption{Trajectory Tracking}
        \label{fig:joint_traj_exp}
    \end{subfigure}

    \begin{subfigure}[b]{0.8\textwidth}
        \centering
        
        \caption{Tracking Errors}
        \label{fig:joint_err_exp}
    \end{subfigure}
    \caption{Joint-Space Experiment Results.}
    \label{fig:joint_exp}
\end{figure}

\subsubsection{Delay and Response Analysis}

To isolate the dynamic performance from the temporal evolution to promote a better visualization of the mentioned
tracking delay, Figure \ref{fig:tracking_delay_exp} presents the input-output correlation (Command vs. Measured
angle) for each joint. An ideal behaviour should be represented by a straight line ($y = x$), while a wider ellipse
would correspond to a higher tracking delay.

Both datasets populates the graph as expected (narrow ellipses for simulation and wider ellipses for the experiment).
Additionally, the slightly wider loops for $q_2$ and $q_3$ correlate with a higher inertial load due to gravity.

\begin{figure}[htbp]
    \centering
    \begin{subfigure}[b]{0.40\textwidth}
        \centering
        
        \caption{Hip ($q_1$)}
    \end{subfigure}
    \begin{subfigure}[b]{0.40\textwidth}
        \centering
        
        \caption{Knee ($q_2$)}
    \end{subfigure}

    \begin{subfigure}[b]{0.40\textwidth}
        \centering
        
        \caption{Ankle ($q_3$)}
    \end{subfigure}
    \caption{Tracking Delay Analysis.}
    \label{fig:tracking_delay_exp}
\end{figure}

\subsubsection{Quantitative Benchmark}

Unexpectedly, the tracking quality performs surprisingly well, despite the fact that the custom servomotor control
algorithm is originally designed for P2P control.

Ultimately, the tracking quality is quantified using the Root Mean Square Error (RMSE) metric (as per Section
\ref{sec:limitations}). Figure \ref{fig:rmse_benchmark} compares the simulation baseline against the physical
prototype.

While the experimental errors are naturally higher than the idealized simulation, the general trend matches for the
two cases, following similar magnitude patterns. The Cartesian RMSE is dominated by the Y-axis ($\approx 5.4$ mm),
consistent with the direction of maximum movement and backlash accumulation.
The main contributor to these errors in the experimental case, as shown in the previous section, was the tracking
delay. Nevertheless, the error remains however remarkably small for a low-cost prototype.

This quantitative benchmark conclusively validates the design approach: the custom actuators and the kinematic
model perform within the requirements defined at the outset of this thesis and well within acceptable limits for
stable locomotion.

\begin{figure}[htbp]
    \centering
    
    \caption{Simulation vs. Experiment Tracking Error.}
    \label{fig:rmse_benchmark}
\end{figure}

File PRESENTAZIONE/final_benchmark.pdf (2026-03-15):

### Performance Benchmark: Commercial vs Custom Design

29.26 | | Motor A
| | | Motor B Smart Actuator
| 23.68

13.41

16.39
14.98

4.44

10.84

15.68
13.48
| 5.27

1.49
| 0.37 | 0.36 | 0.37 | 0.65
Max Abs Err | Fwd RMSE | Bwd RMSE | Global RMSE | Avg Hysteresis

0

5

10

15

20

25

30

### Error Magnitude (deg)

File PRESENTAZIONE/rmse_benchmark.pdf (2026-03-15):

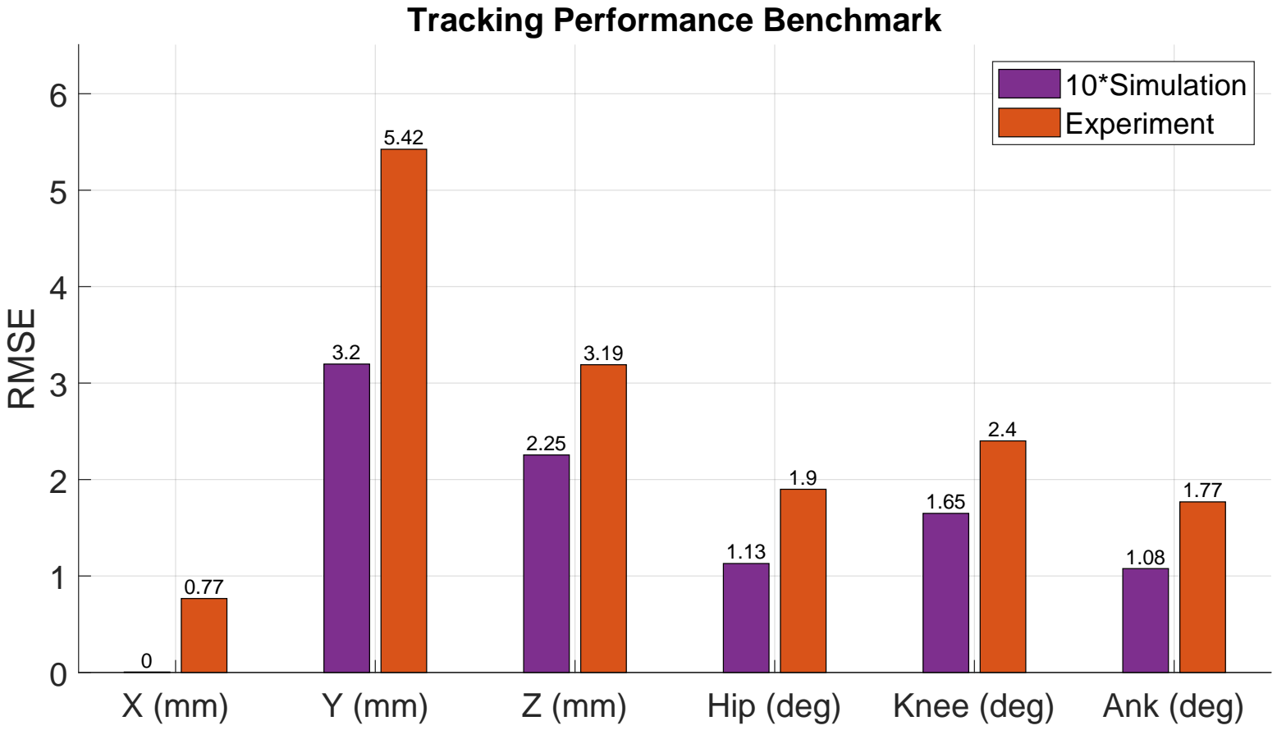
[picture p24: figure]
Hip (deg); Knee (deg); Ank (deg); RMSE; Tracking Performance Benchmark; 10*Simulation Experiment

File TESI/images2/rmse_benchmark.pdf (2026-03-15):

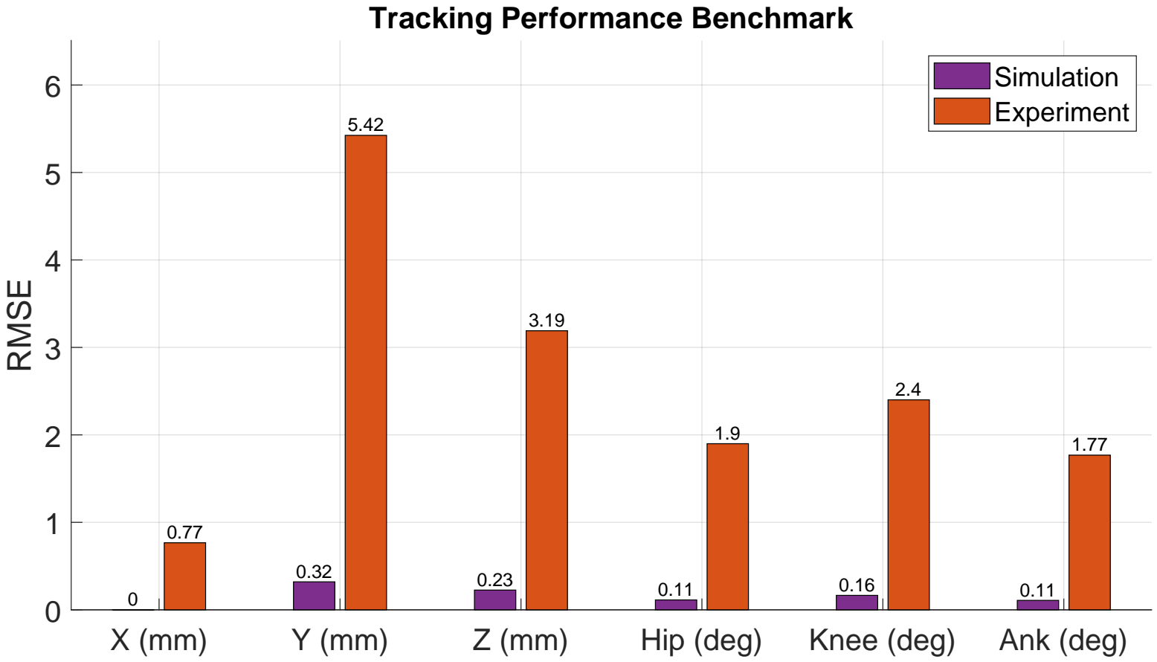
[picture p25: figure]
Hip (deg); Knee (deg); Ank (deg); RMSE; Tracking Performance Benchmark; Simulation Experiment

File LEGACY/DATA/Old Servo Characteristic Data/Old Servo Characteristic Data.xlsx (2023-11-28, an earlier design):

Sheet: Dati Servo A
Pulse Width [#] | Duty Cycle [%] | Ton [ms] | Expected Angle [°] | Measured Angle [#] | Adjusted Measure [#] | Measured Angle [°] | Useful Value [bool] | Measured Angle Reverse [#] | Adjusted Measure Reversed [#] | Measured Angle Reversed [°] | Hysteresis [°] | Error [°] | Error Reversed [°] | Steps [#]: | 4096 | Total number of PWM steps realizable
 |  |  |  |  |  |  |  |  |  |  |  |  |  | Frequency [Hz]: | 50 | PWM Frequency
102 | 2.49 | 0.498 | 0.000 | 1715 | 0 | 0.000 |  | 1739 | 24 | 2.109 | 2.109 | 0.000 | -2.109 |  |  | Total output shaft swing
103 | 2.51 | 0.503 | 0.000 | 1715 | 0 | 0.000 |  | 1753 | 38 | 3.340 | 3.340 | 0.000 | -3.340 | Swing [°]: | 225.615 | Total number of tested steps
104 | 2.54 | 0.508 | 0.000 | 1715 | 0 | 0.000 |  | 1763 | 48 | 4.219 | 4.219 | 0.000 | -4.219 | Working Steps [#]: | 358
105 | 2.56 | 0.513 | 0.000 | 1715 | 0 | 0.000 |  | 1775 | 60 | 5.273 | 5.273 | 0.000 | -5.273
106 | 2.59 | 0.518 | 0.000 | 1715 | 0 | 0.000 |  | 1783 | 68 | 5.977 | 5.977 | 0.000 | -5.977 |  |  | Green = Input
107 | 2.61 | 0.522 | 0.000 | 1715 | 0 | 0.000 |  | 1792 | 77 | 6.768 | 6.768 | 0.000 | -6.768 |  |  | Orange = Measure
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

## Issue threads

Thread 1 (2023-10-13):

Modello ponte H

PippoGot, 2023-10-13:
Il modello del ponte H attuale non funziona come dovrebbe, in particolare i mosfet sembrano avere dei parametri sbagliati, la tensione ai loro capi risulta corretta, ma la corrente no.

potrebbe essere un problema della modellazione del diodo di ricircolo interno al mosfet.

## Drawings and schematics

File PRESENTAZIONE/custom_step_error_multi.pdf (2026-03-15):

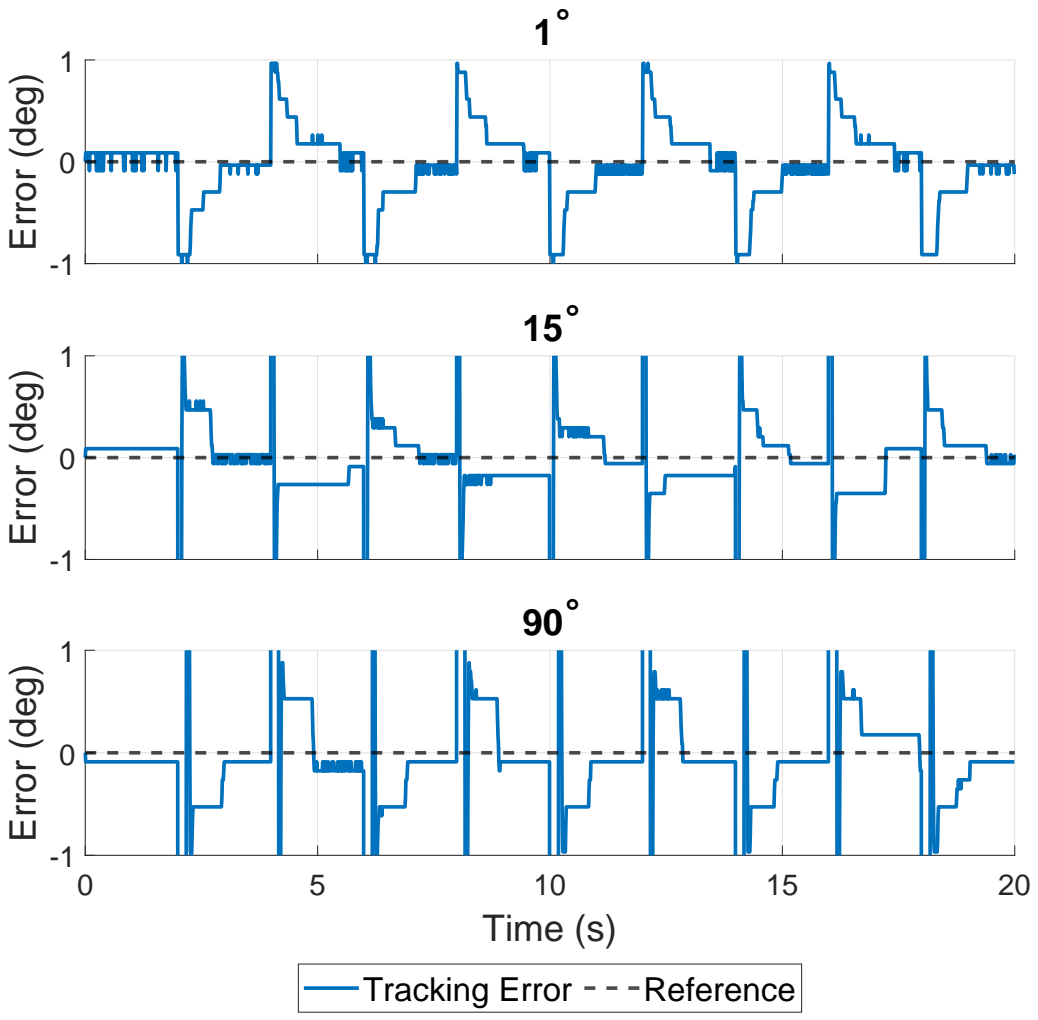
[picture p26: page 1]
Error (deg); Time (s); Tracking Error; Reference

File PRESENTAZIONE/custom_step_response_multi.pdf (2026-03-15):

1

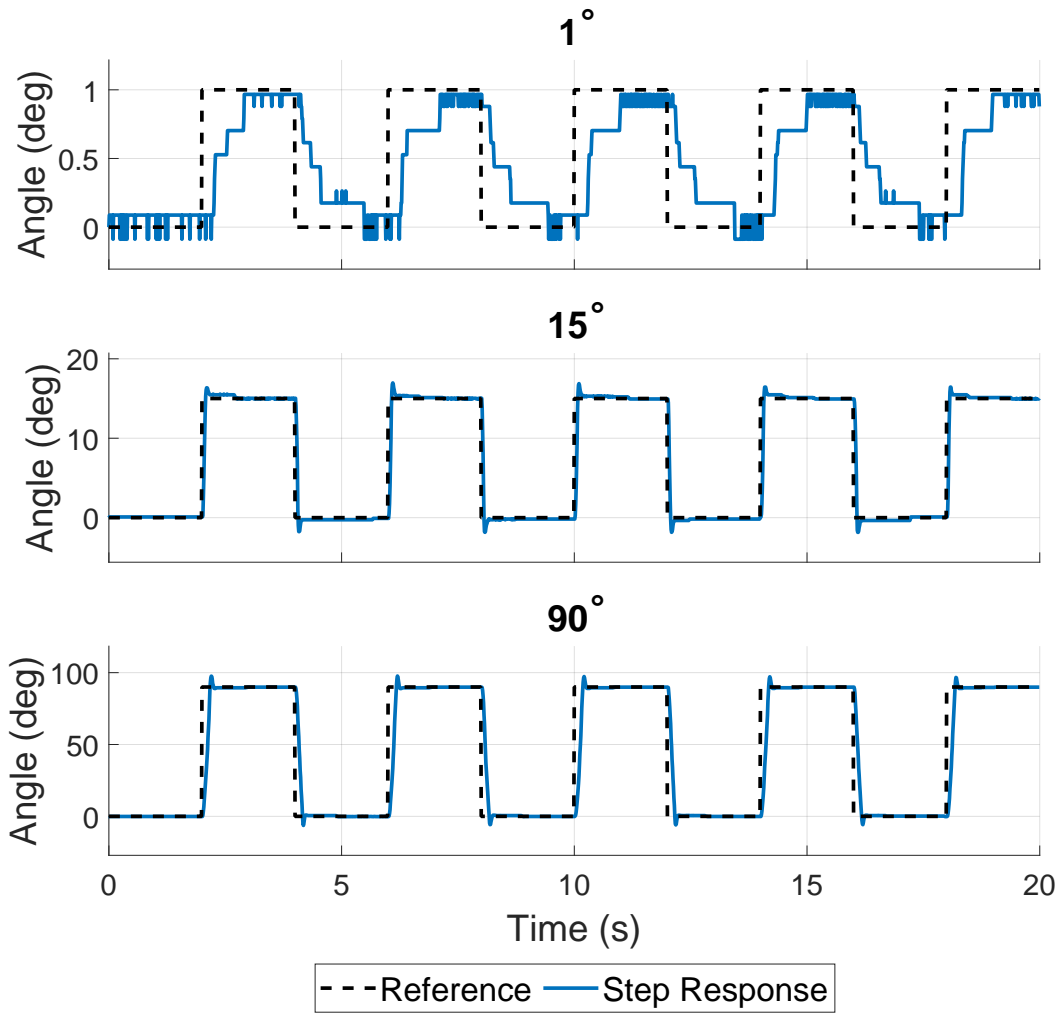
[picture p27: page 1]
Angle (deg); Time (s); Reference; Step Response

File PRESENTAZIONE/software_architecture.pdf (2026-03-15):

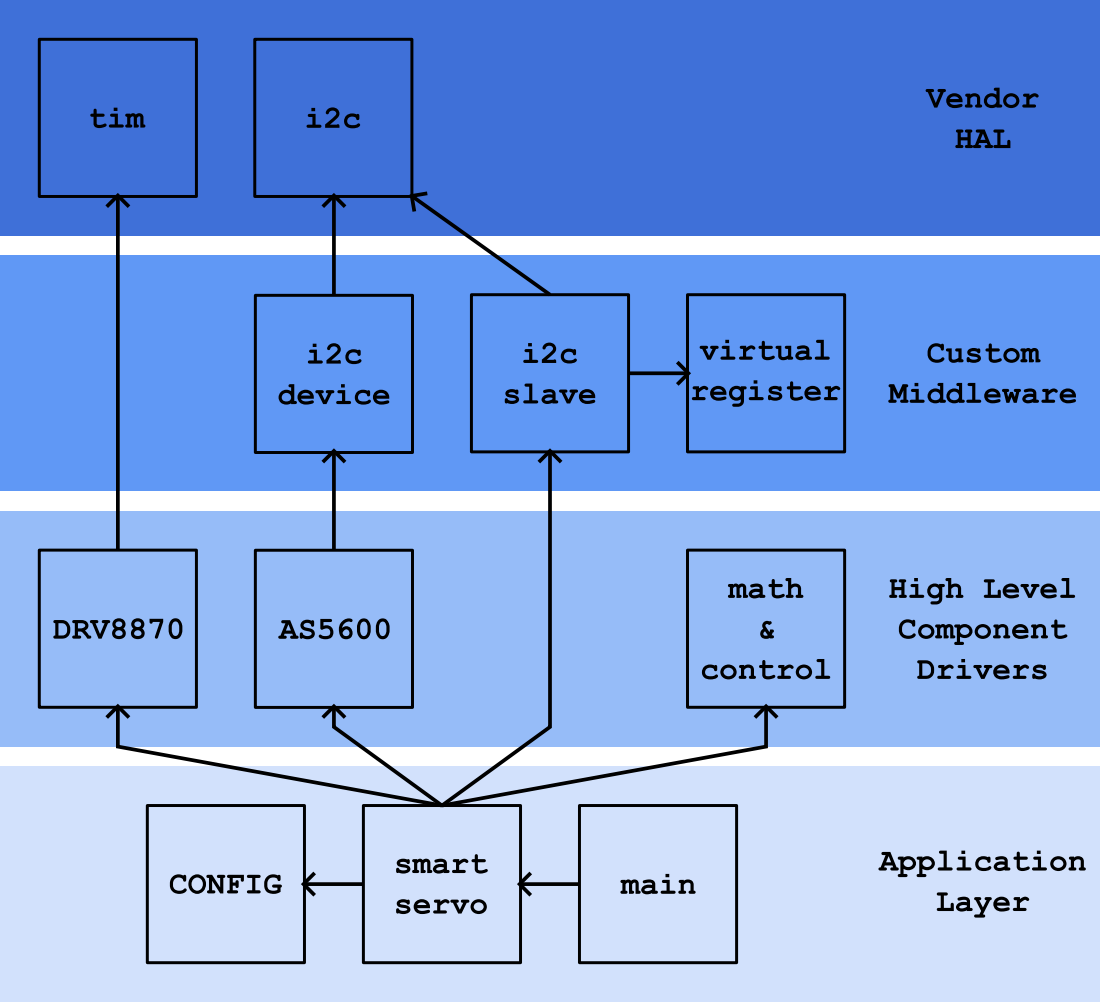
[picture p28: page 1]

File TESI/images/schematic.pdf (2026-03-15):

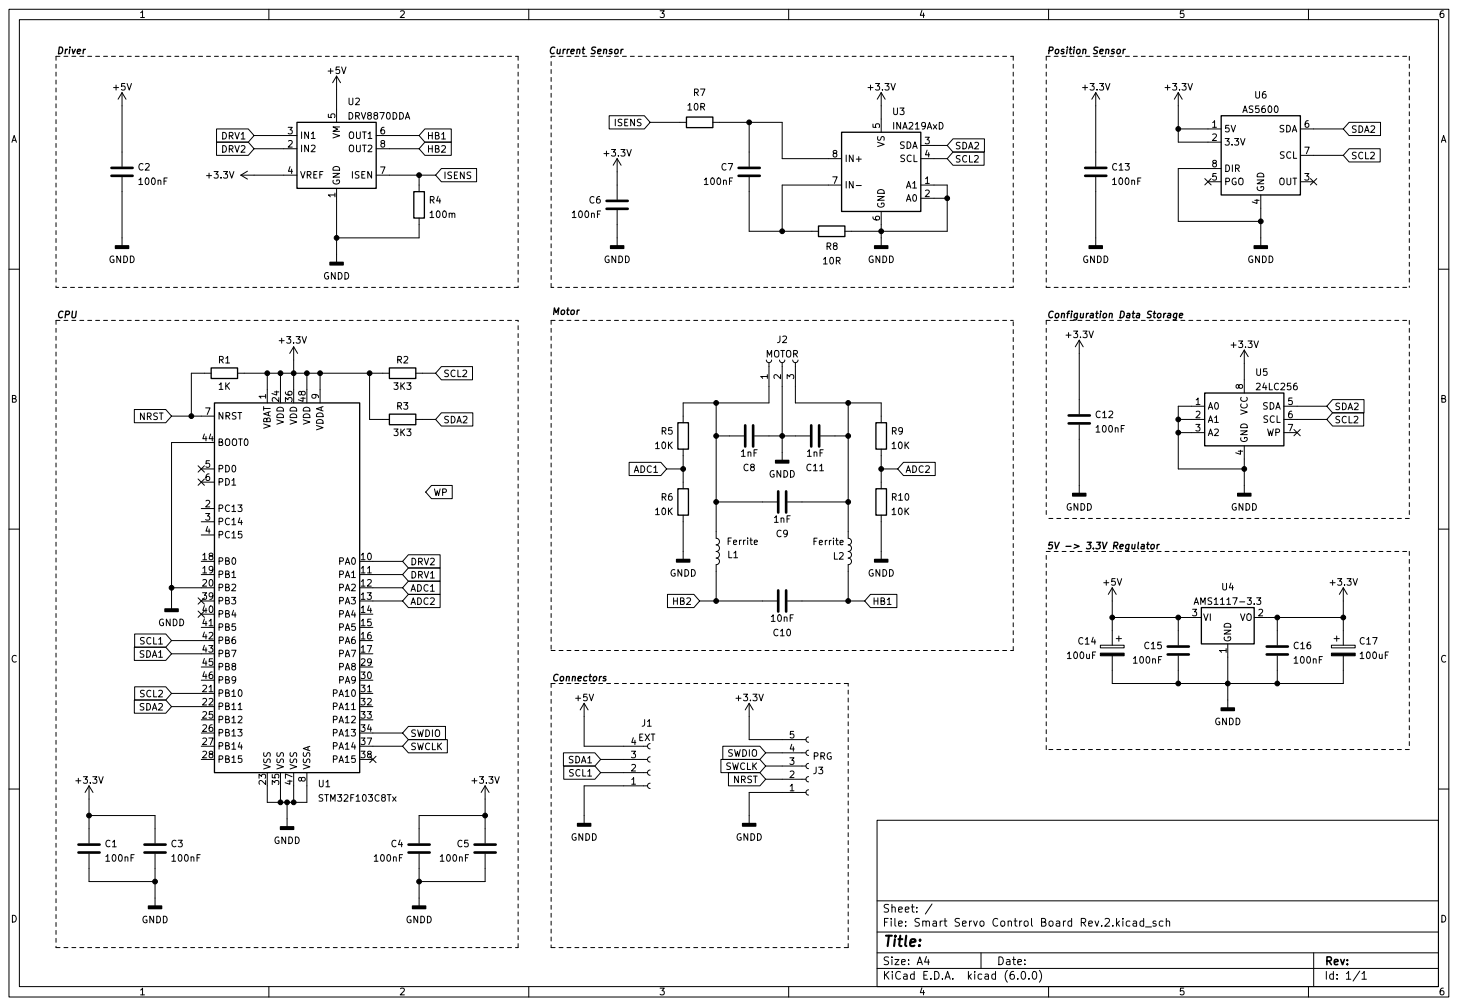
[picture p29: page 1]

4 PGO 5 SDA 6 SCL 7 DIR 8 U6 AS5600 +3.3V R2

1 PA0 10 PA1 11 PA2 12 PA3 13 PA4 14 PA5 15 PA6 16 PA7 17 PB0 18 PB1 19 PC13 2 PB2 20 PB10 21 PB11 22 VSS 23 VDD 24 PB12 25 PB13 26 PB14 27 PB15 28 PA8 29 PC14 3 PA9 30 PA10 31 PA11 32 PA12 33 PA13 34 VSS 35 VDD 36 PA14 37 PA15 38 PB3 39 PC15 4 PB4 40 PB5 41 PB6 42 PB7 43 BOOT0 44 PB8 45 PB9 46 VSS 47 VDD 48 PD0 5 PD1 6 NRST 7 VSSA

4 SDA 5 SCL 6 WP 7 VCC

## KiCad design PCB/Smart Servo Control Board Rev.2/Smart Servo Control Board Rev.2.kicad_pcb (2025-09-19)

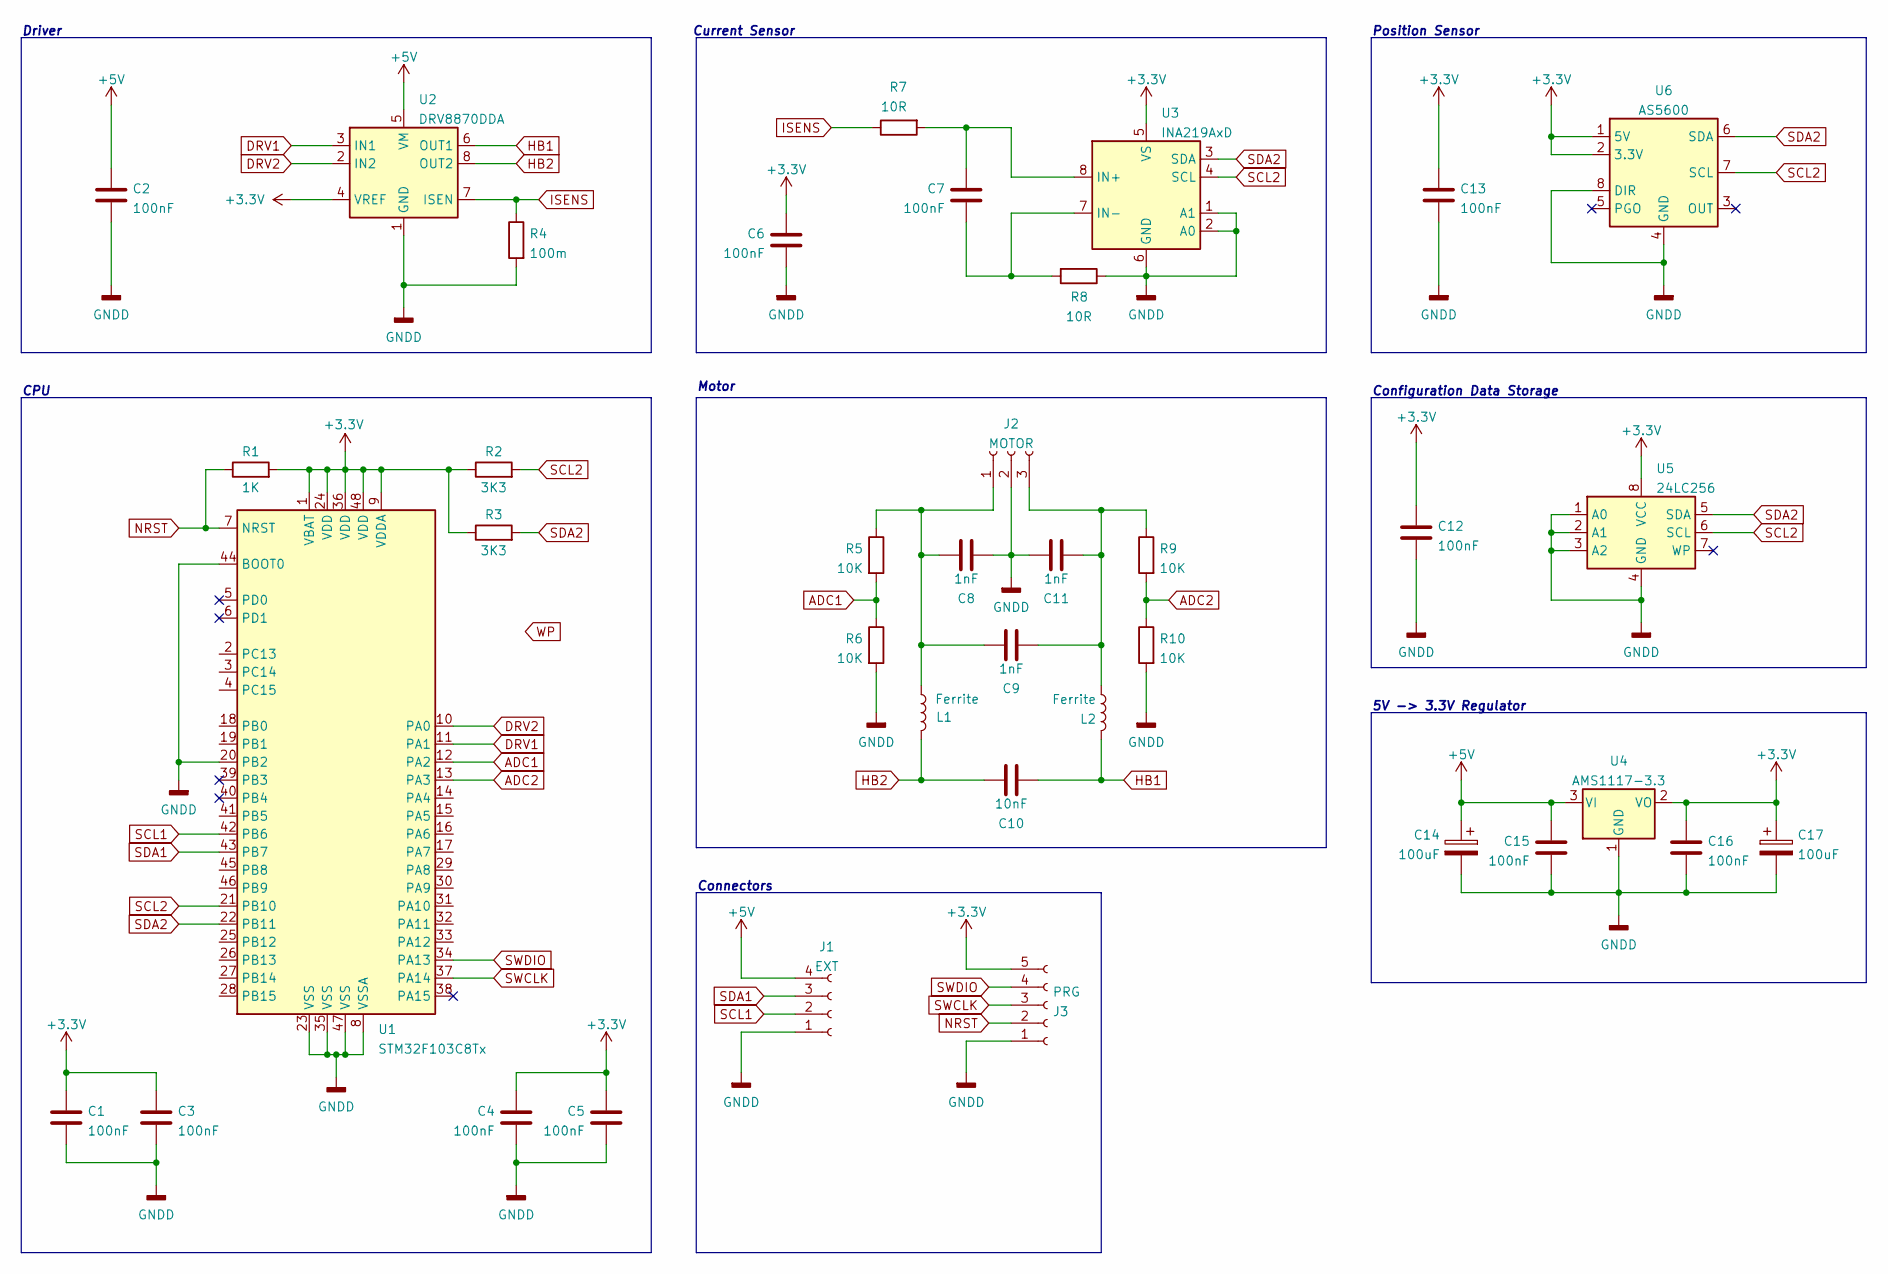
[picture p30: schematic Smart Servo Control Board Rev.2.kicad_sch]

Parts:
C1, C2, C3, C4, C5, C6, C7, C12, C13, C15, C16: 100nF; R_0603_1608Metric_Pad0.98x0.95mm_HandSolder
C8, C9, C11: 1nF; R_0603_1608Metric_Pad0.98x0.95mm_HandSolder
C10: 10nF; R_0603_1608Metric_Pad0.98x0.95mm_HandSolder
C14, C17: 100uF; CP_EIA-3216-10_Kemet-I
J1: EXT; Pad_1x04_P2.54mm_Vertical
J2: MOTOR; DC motor 17mm
J3: PRG; PinHeader_1x05_P2.54mm_Vertical_SMD_Pin1Left
L1, L2: Ferrite; R_0603_1608Metric_Pad0.98x0.95mm_HandSolder
R1: 1K; R_0603_1608Metric_Pad0.98x0.95mm_HandSolder
R2, R3: 3K3; R_0603_1608Metric_Pad0.98x0.95mm_HandSolder
R4: 100m; R_1206_3216Metric_Pad1.30x1.75mm_HandSolder
R5, R6, R9, R10: 10K; R_0603_1608Metric_Pad0.98x0.95mm_HandSolder
R7, R8: 10R; R_0603_1608Metric_Pad0.98x0.95mm_HandSolder
U1: STM32F103C8Tx; LQFP-48_7x7mm_P0.5mm
U2: DRV8870DDA; SOIC-8-1EP_3.9x4.9mm_P1.27mm_EP2.514x3.2mm
U3: INA219AxD; SOT-23-8
U4: AMS1117-3.3; SOT-223-3_TabPin2
U5: 24LC256; SO-8_3.9x4.9mm_P1.27mm
U6: AS5600; SO-8_3.9x4.9mm_P1.27mm

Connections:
+3V3: C1.2, C3.2, C4.2, C5.2, C6.2, C12.2, C13.2, C16.1, C17.1, J3.5, R1.2, R2.1, R3.1, U1.1 (VBAT), U1.9 (VDDA), U1.24 (VDD), U1.36 (VDD), U1.48 (VDD), U2.4 (VREF), U3.5 (VS), U4.2 (VO), U5.8 (VCC), U6.1 (5V), U6.2 (3.3V)
+5V: C2.2, C14.1, C15.1, J1.4, U2.5 (VM), U4.3 (VI)
ADC1: R5.2, R6.1, U1.12 (PA2)
ADC2: R9.2, R10.1, U1.13 (PA3)
DRV1: U1.11 (PA1), U2.3 (IN1)
DRV2: U1.10 (PA0), U2.2 (IN2)
GNDD: C1.1, C2.1, C3.1, C4.1, C5.1, C6.1, C8.2, C11.1, C12.1, C13.1, C14.2, C15.2, C16.2, C17.2, J1.1, J2.2, J3.1, R4.2, R6.2, R8.1, R10.2, U1.8 (VSSA), U1.20 (PB2), U1.23 (VSS), U1.35 (VSS), U1.44 (BOOT0), U1.47 (VSS), U2.1 (GND), U2.9 (GND), U3.1 (A1), U3.2 (A0), U3.6 (GND), U4.1 (GND), U5.1 (A0), U5.2 (A1), U5.3 (A2), U5.4 (GND), U6.4 (GND), U6.8 (DIR)
HB1: C10.2, L2.2, U2.6 (OUT1)
HB2: C10.1, L1.2, U2.8 (OUT2)
ISENS: R4.1, R7.1, U2.7 (ISEN)
NRST: J3.2, R1.1, U1.7 (NRST)
unnamed: C7.1, R7.2, U3.8 (IN+)
unnamed: C7.2, R8.2, U3.7 (IN-)
unnamed: C8.1, C9.1, J2.1, L1.1, R5.1
unnamed: C9.2, C11.2, J2.3, L2.1, R9.1
SCL1: J1.2, U1.42 (PB6)
SCL2: R2.2, U1.21 (PB10), U3.4 (SCL), U5.6 (SCL), U6.7 (SCL)
SDA1: J1.3, U1.43 (PB7)
SDA2: R3.2, U1.22 (PB11), U3.3 (SDA), U5.5 (SDA), U6.6 (SDA)
SWCLK: J3.3, U1.37 (PA14)
SWDIO: J3.4, U1.34 (PA13)

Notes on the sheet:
Current Sensor
Position Sensor
Motor
5V -> 3.3V Regulator
Driver
CPU
Connectors
Configuration Data Storage

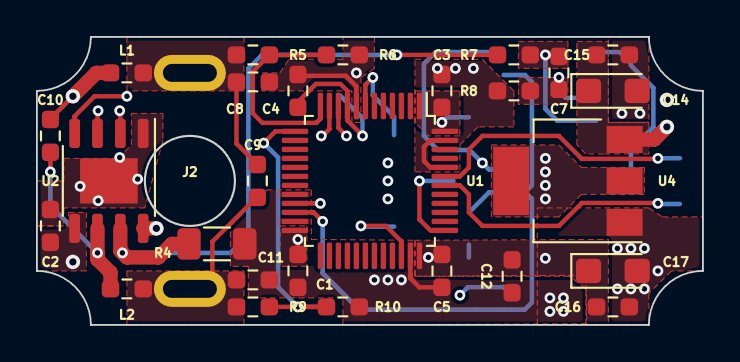
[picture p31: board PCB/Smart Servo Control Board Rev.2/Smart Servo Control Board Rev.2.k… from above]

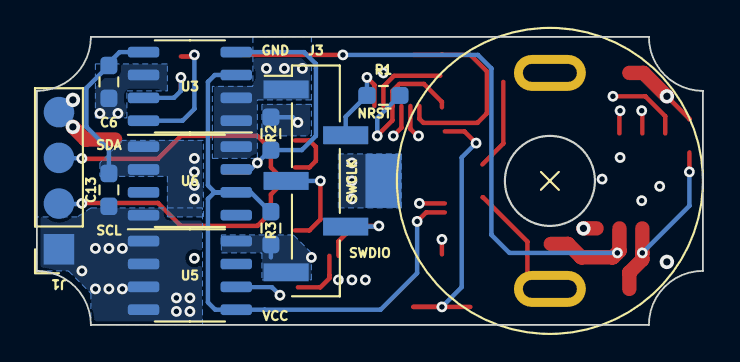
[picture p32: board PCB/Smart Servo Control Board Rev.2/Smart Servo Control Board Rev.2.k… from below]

Board: 4 copper layers, 37.0 x 16.0 mm, 38 parts (10 on the bottom side), 21 nets.

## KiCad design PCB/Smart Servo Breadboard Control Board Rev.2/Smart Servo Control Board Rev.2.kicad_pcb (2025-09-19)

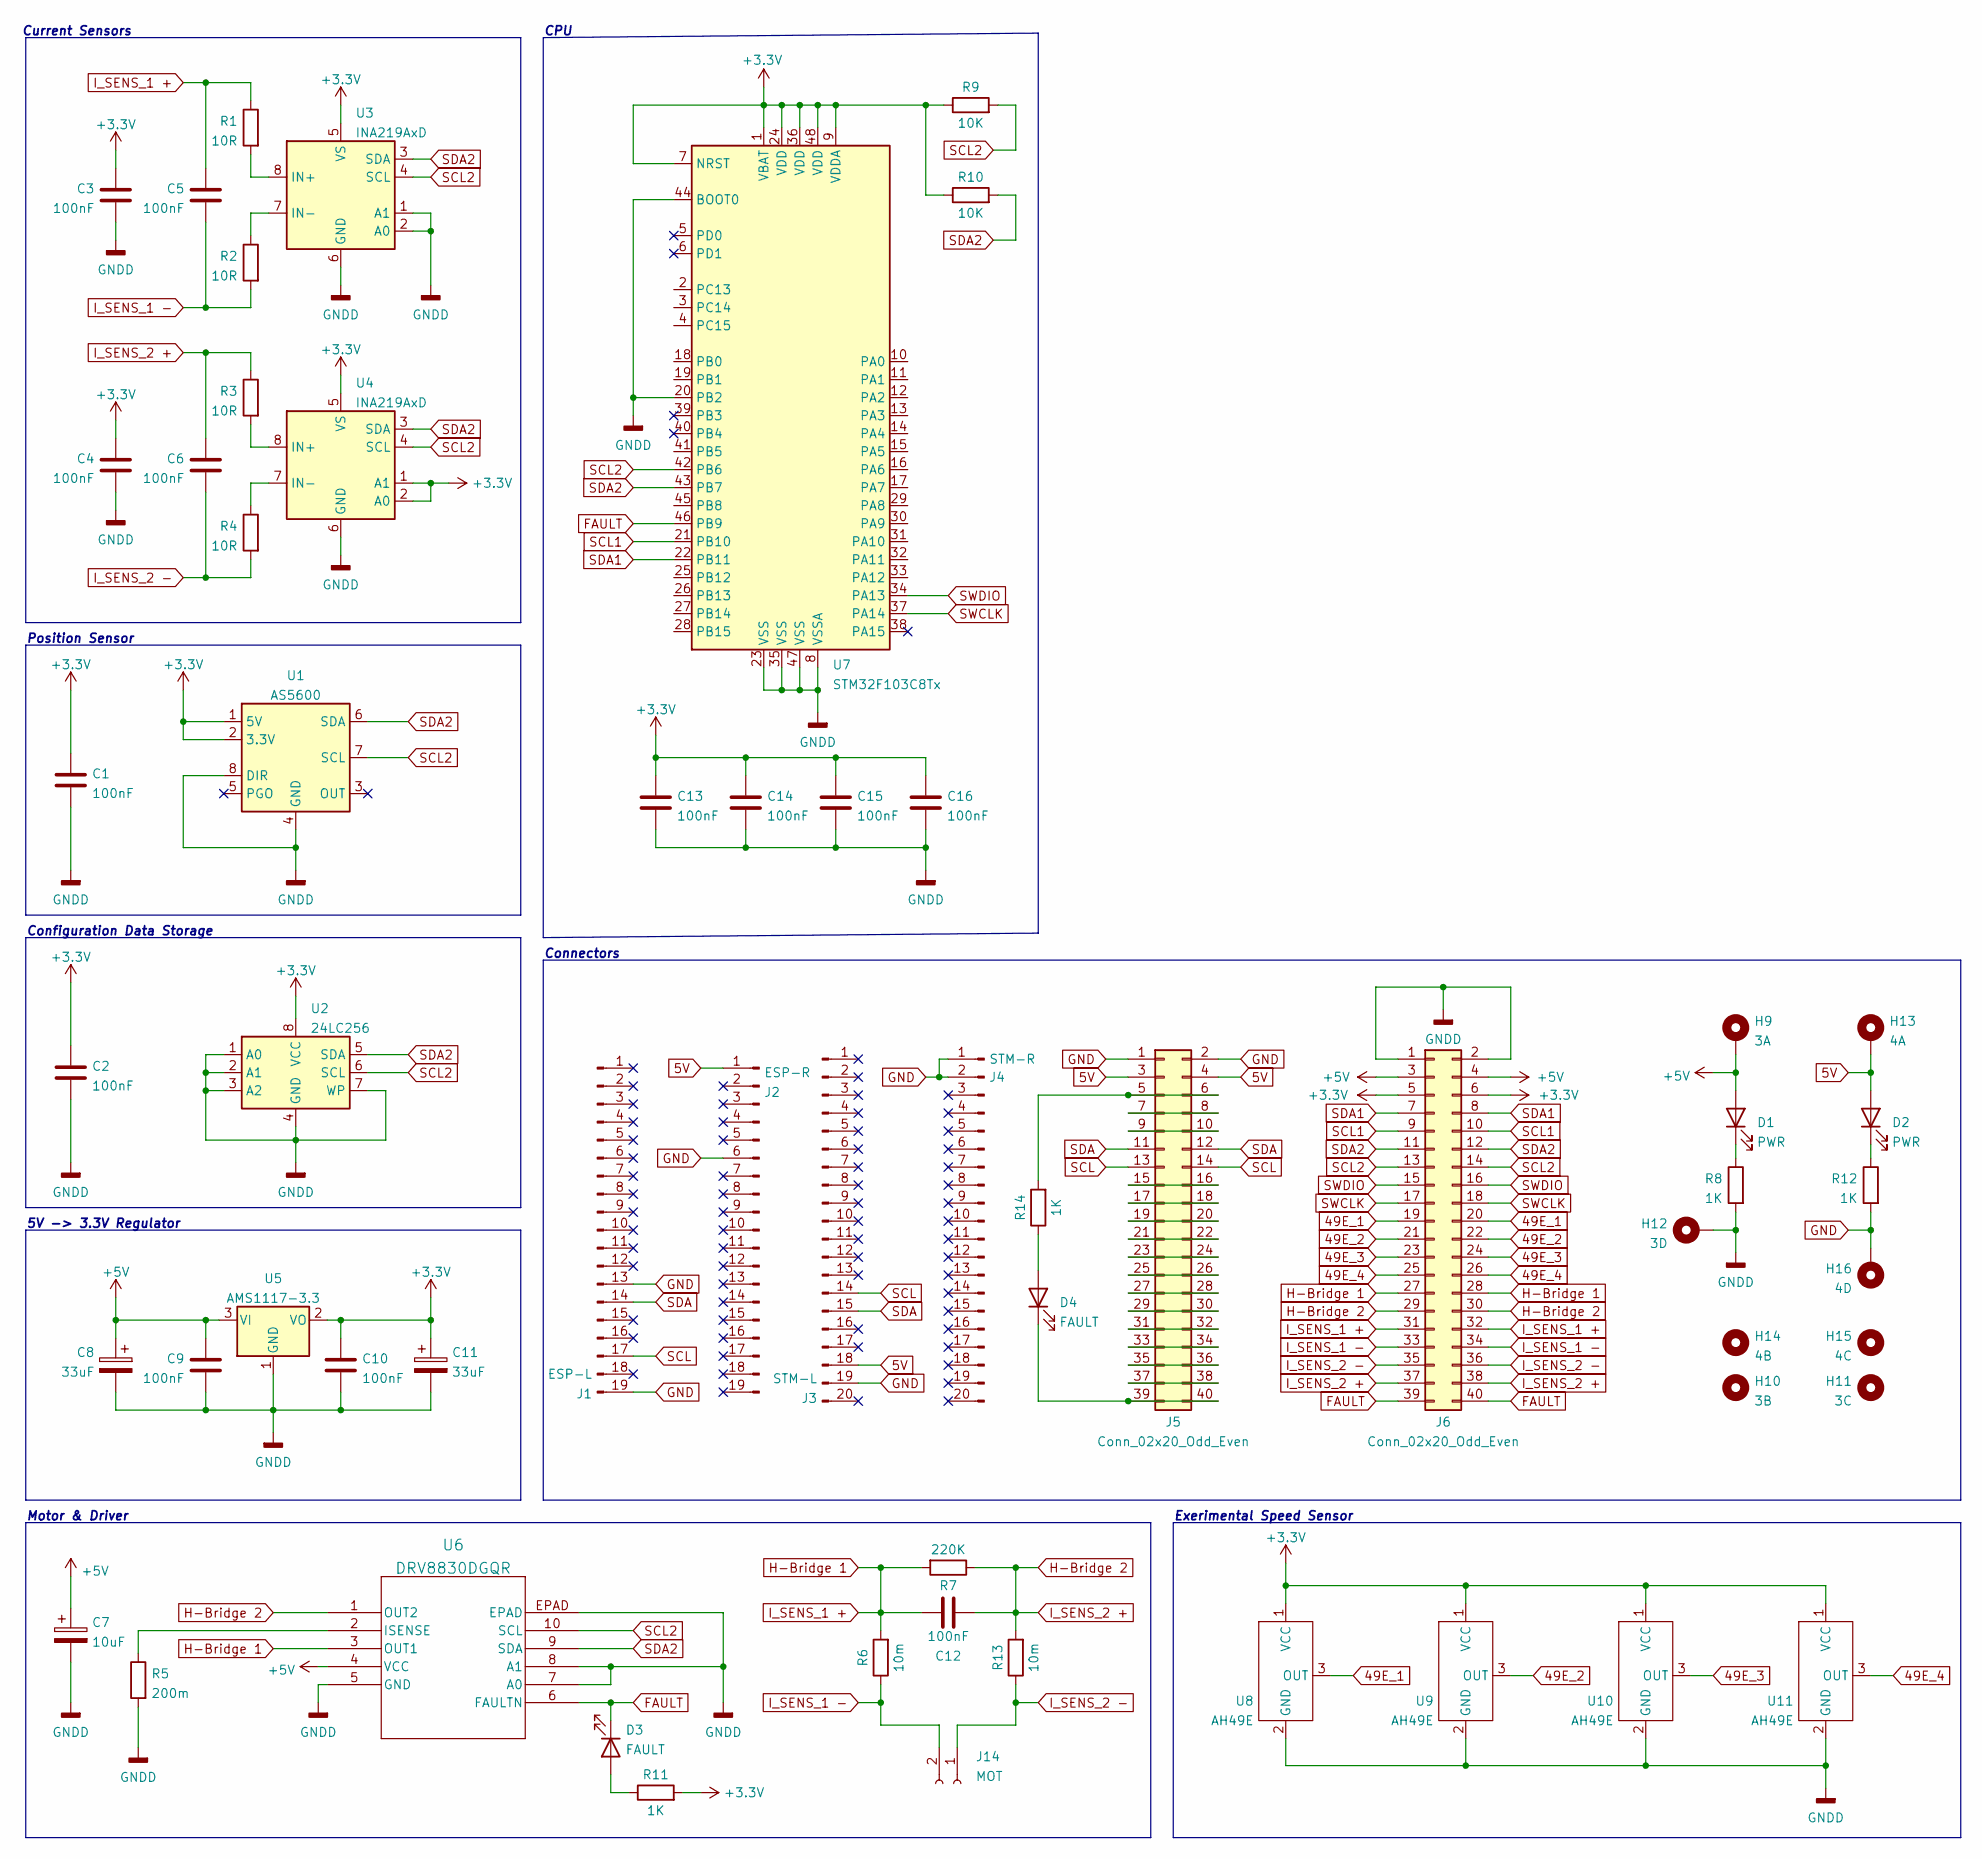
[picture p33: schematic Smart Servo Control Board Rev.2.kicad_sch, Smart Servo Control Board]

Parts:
C1, C2, C3, C4, C5, C6, C9, C10, C12, C13, C14, C15, C16: 100nF; R_0603_1608Metric_Pad0.98x0.95mm_HandSolder
C7: 10uF; R_0603_1608Metric_Pad0.98x0.95mm_HandSolder
C8, C11: 33uF; R_0603_1608Metric_Pad0.98x0.95mm_HandSolder
D1, D2: PWR; D_1206_3216Metric_Pad1.42x1.75mm_HandSolder
D3, D4: FAULT; D_1206_3216Metric_Pad1.42x1.75mm_HandSolder
H9: 3A; MountingHole_4.3mm_M4_DIN965_Pad_TopBottom
H10: 3B; MountingHole_4.3mm_M4
H11: 3C; MountingHole_4.3mm_M4
H12: 3D; MountingHole_4.3mm_M4_DIN965_Pad_TopBottom
H13: 4A; MountingHole_4.3mm_M4_DIN965_Pad_TopBottom
H14: 4B; MountingHole_4.3mm_M4
H15: 4C; MountingHole_4.3mm_M4
H16: 4D; MountingHole_4.3mm_M4_DIN965_Pad_TopBottom
J1: ESP-L; PinSocket_1x19_P2.54mm_Vertical
J2: ESP-R; PinSocket_1x19_P2.54mm_Vertical
J3: STM-L; PinSocket_1x20_P2.54mm_Vertical
J4: STM-R; PinSocket_1x20_P2.54mm_Vertical
J5, J6: Conn_02x20_Odd_Even; PinSocket_2x20_P2.54mm_Vertical
J14: MOT; PinSocket_1x02_P2.54mm_Vertical
R1, R2, R3, R4: 10R; R_0603_1608Metric_Pad0.98x0.95mm_HandSolder
R5: 200m; R_1206_3216Metric_Pad1.30x1.75mm_HandSolder
R6, R13: 10m; R_0603_1608Metric_Pad0.98x0.95mm_HandSolder
R7: 220K; R_0603_1608Metric_Pad0.98x0.95mm_HandSolder
R8, R11, R12, R14: 1K; R_0603_1608Metric_Pad0.98x0.95mm_HandSolder
R9, R10: 10K; R_0603_1608Metric_Pad0.98x0.95mm_HandSolder
U1: AS5600; SO-8_3.9x4.9mm_P1.27mm
U2: 24LC256; SO-8_3.9x4.9mm_P1.27mm
U3, U4: INA219AxD; SOIC-8_3.9x4.9mm_P1.27mm
U5: AMS1117-3.3; SOT-223-3_TabPin2
U6: DRV8830DGQR; DGQ10_2P18X1P72
U7: STM32F103C8Tx; LQFP-48_7x7mm_P0.5mm
U8, U9: AH49E; TO-92S
U10, U11: AH49E; SOT-23

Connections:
5V: D2.2 (A), H13.1, J2.1, J3.18, J5.3, J5.4
49E_1: J6.19, J6.20, U8.3 (OUT)
49E_2: J6.21, J6.22, U9.3 (OUT)
49E_3: J6.23, J6.24, U10.3 (OUT)
49E_4: J6.25, J6.26, U11.3 (OUT)
+3V3: C1.2, C2.2, C3.2, C4.2, C10.1, C11.1, C13.2, C14.2, C15.2, C16.2, J6.5, J6.6, R9.1, R10.1, R11.2, U1.1 (5V), U1.2 (3.3V), U2.8 (VCC), U3.5 (VS), U4.1 (A1), U4.2 (A0), U4.5 (VS), U5.2 (VO), U7.1 (VBAT), U7.7 (NRST), U7.9 (VDDA), U7.24 (VDD), U7.36 (VDD), U7.48 (VDD), U8.1 (VCC), U9.1 (VCC), U10.1 (VCC), U11.1 (VCC)
+5V: C7.1, C8.1, C9.1, D1.2 (A), H9.1, J6.3, J6.4, U5.3 (VI), U6.4 (VCC)
FAULT: D3.1 (K), J6.39, J6.40, U6.6 (FAULTN), U7.46 (PB9)
GND: H16.1, J1.13, J1.19, J2.6, J3.19, J4.1, J4.2, J5.1, J5.2, R12.2
GNDD: C1.1, C2.1, C3.1, C4.1, C7.2, C8.2, C9.2, C10.2, C11.2, C13.1, C14.1, C15.1, C16.1, H12.1, J6.1, J6.2, R5.2, R8.2, U1.4 (GND), U1.8 (DIR), U2.1 (A0), U2.2 (A1), U2.3 (A2), U2.4 (GND), U2.7 (WP), U3.1 (A1), U3.2 (A0), U3.6 (GND), U4.6 (GND), U5.1 (GND), U6.5 (GND), U6.7 (A0), U6.8 (A1), U6.EPAD, U6.V, U7.8 (VSSA), U7.20 (PB2), U7.23 (VSS), U7.35 (VSS), U7.44 (BOOT0), U7.47 (VSS), U8.2 (GND), U9.2 (GND), U10.2 (GND), U11.2 (GND)
H-Bridge 1: C5.1, C12.1, J6.27, J6.28, J6.31, J6.32, R1.1, R6.2, R7.2, U6.3 (OUT1)
H-Bridge 2: C6.1, C12.2, J6.29, J6.30, J6.37, J6.38, R3.1, R7.1, R13.2, U6.1 (OUT2)
I_SENS_1 -: C5.2, J6.33, J6.34, J14.2, R2.2, R6.1
I_SENS_2 -: C6.2, J6.35, J6.36, J14.1, R4.2, R13.1
unnamed: D1.1 (K), R8.1
unnamed: D2.1 (K), R12.1
unnamed: D3.2 (A), R11.1
unnamed: D4.2 (A), R14.1
unnamed: J5.5, J5.6, R14.2
unnamed: J5.7, J5.8
unnamed: J5.9, J5.10
unnamed: J5.15, J5.16
unnamed: J5.17, J5.18
unnamed: J5.19, J5.20
unnamed: J5.21, J5.22
unnamed: J5.23, J5.24
unnamed: J5.25, J5.26
unnamed: J5.27, J5.28
unnamed: J5.29, J5.30
unnamed: J5.31, J5.32
unnamed: J5.33, J5.34
unnamed: J5.35, J5.36
unnamed: J5.37, J5.38
unnamed: D4.1 (K), J5.39, J5.40
unnamed: R1.2, U3.8 (IN+)
unnamed: R2.1, U3.7 (IN-)
unnamed: R3.2, U4.8 (IN+)
unnamed: R4.1, U4.7 (IN-)
unnamed: R5.1, U6.2 (ISENSE)
SCL: J1.17, J3.14, J5.13, J5.14
SCL1: J6.9, J6.10, U7.21 (PB10)
SCL2: J6.13, J6.14, R9.2, U1.7 (SCL), U2.6 (SCL), U3.4 (SCL), U4.4 (SCL), U6.10 (SCL), U7.42 (PB6)
SDA: J1.14, J3.15, J5.11, J5.12
SDA1: J6.7, J6.8, U7.22 (PB11)
SDA2: J6.11, J6.12, R10.2, U1.6 (SDA), U2.5 (SDA), U3.3 (SDA), U4.3 (SDA), U6.9 (SDA), U7.43 (PB7)
SWCLK: J6.17, J6.18, U7.37 (PA14)
SWDIO: J6.15, J6.16, U7.34 (PA13)

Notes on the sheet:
Configuration Data Storage
Position Sensor
CPU
Motor & Driver
5V -> 3.3V Regulator
Current Sensors
Connectors
Exerimental Speed Sensor

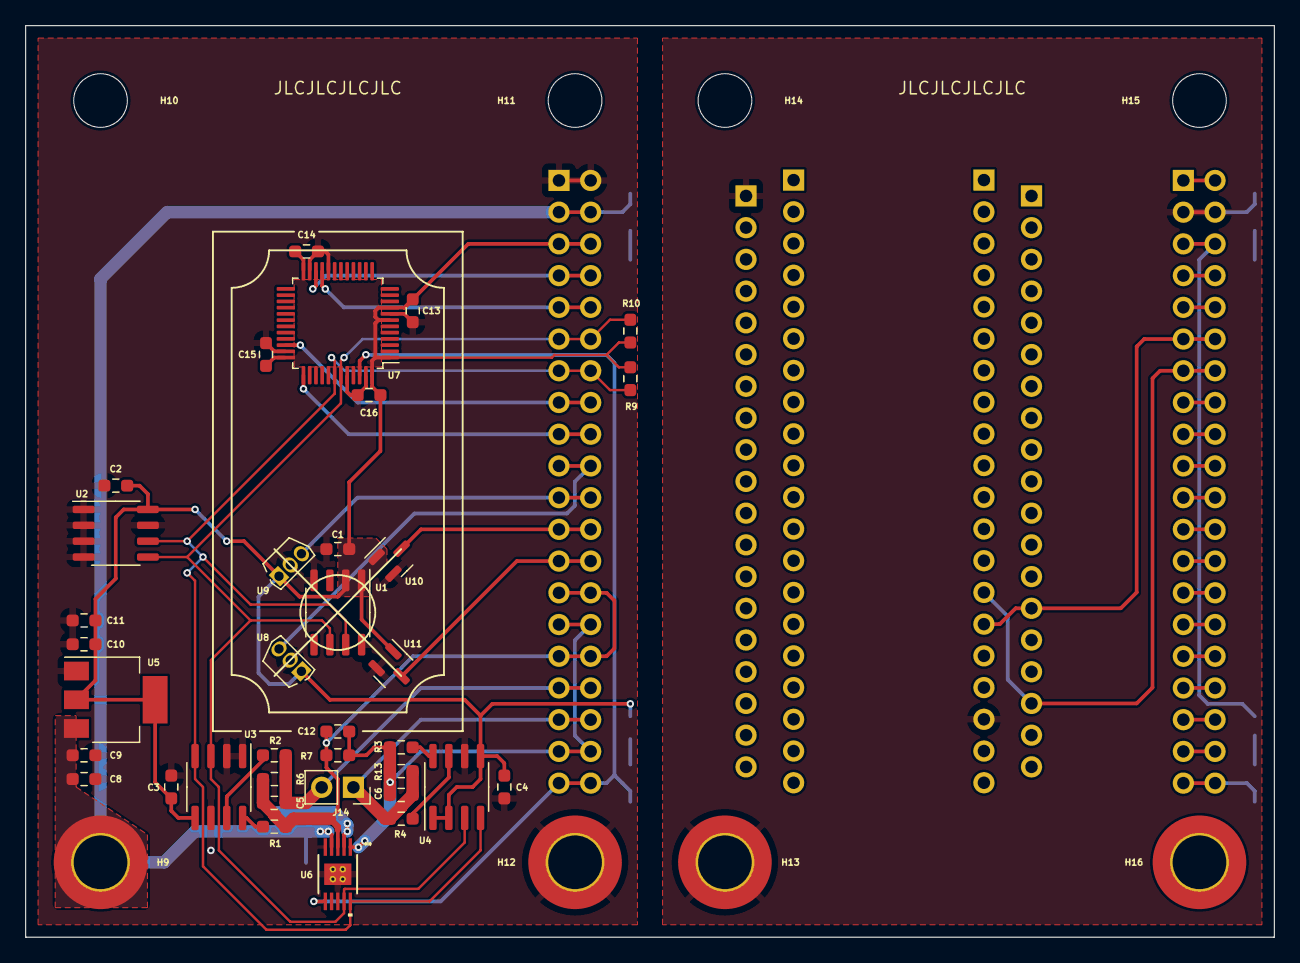
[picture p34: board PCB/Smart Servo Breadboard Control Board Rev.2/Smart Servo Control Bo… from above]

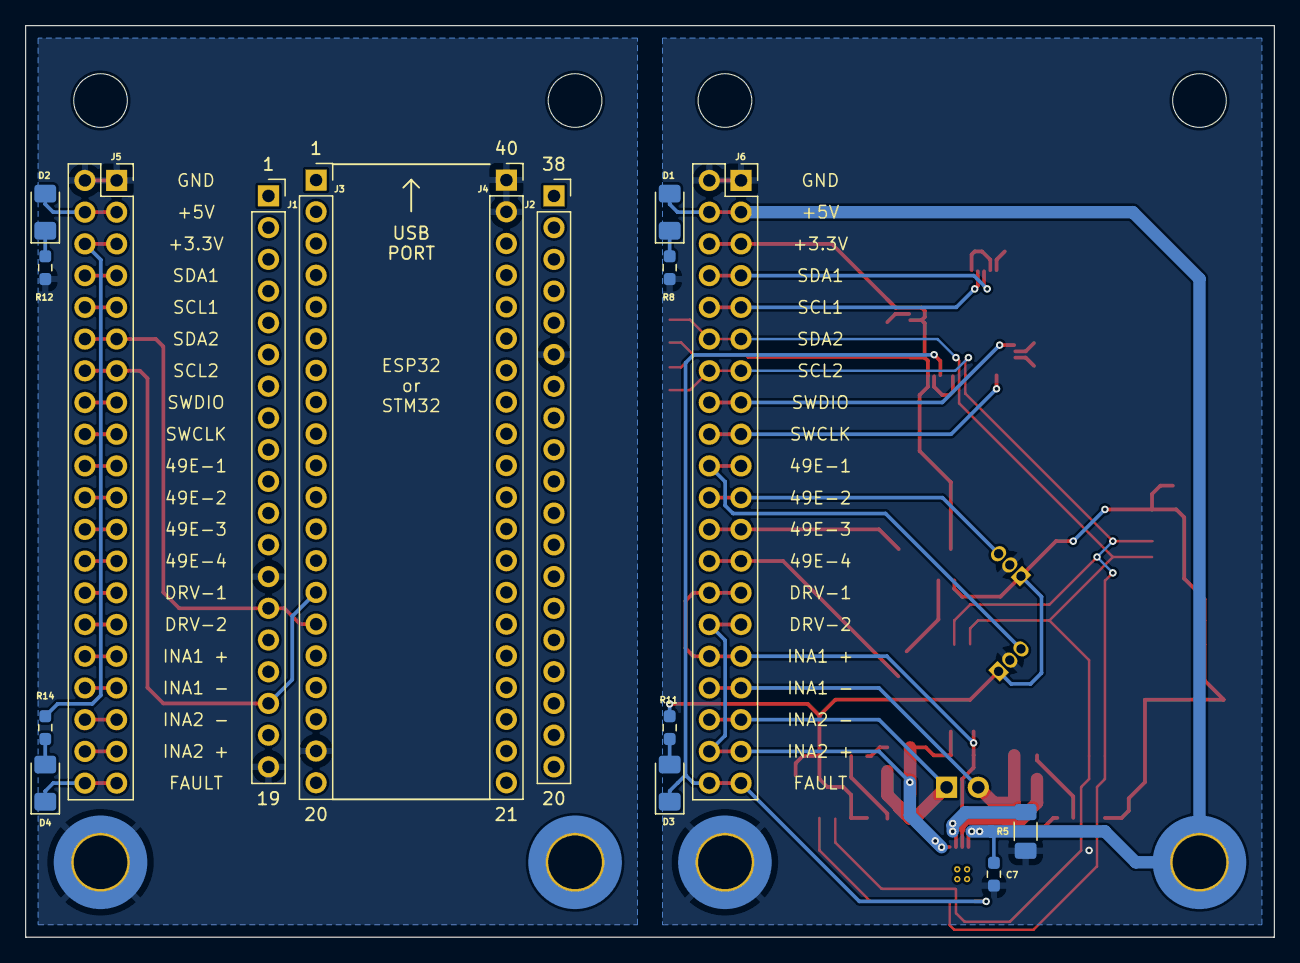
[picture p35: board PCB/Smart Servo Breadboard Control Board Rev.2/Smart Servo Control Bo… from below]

Board: 4 copper layers, 100.0 x 73.0 mm, 60 parts (16 on the bottom side), 47 nets.

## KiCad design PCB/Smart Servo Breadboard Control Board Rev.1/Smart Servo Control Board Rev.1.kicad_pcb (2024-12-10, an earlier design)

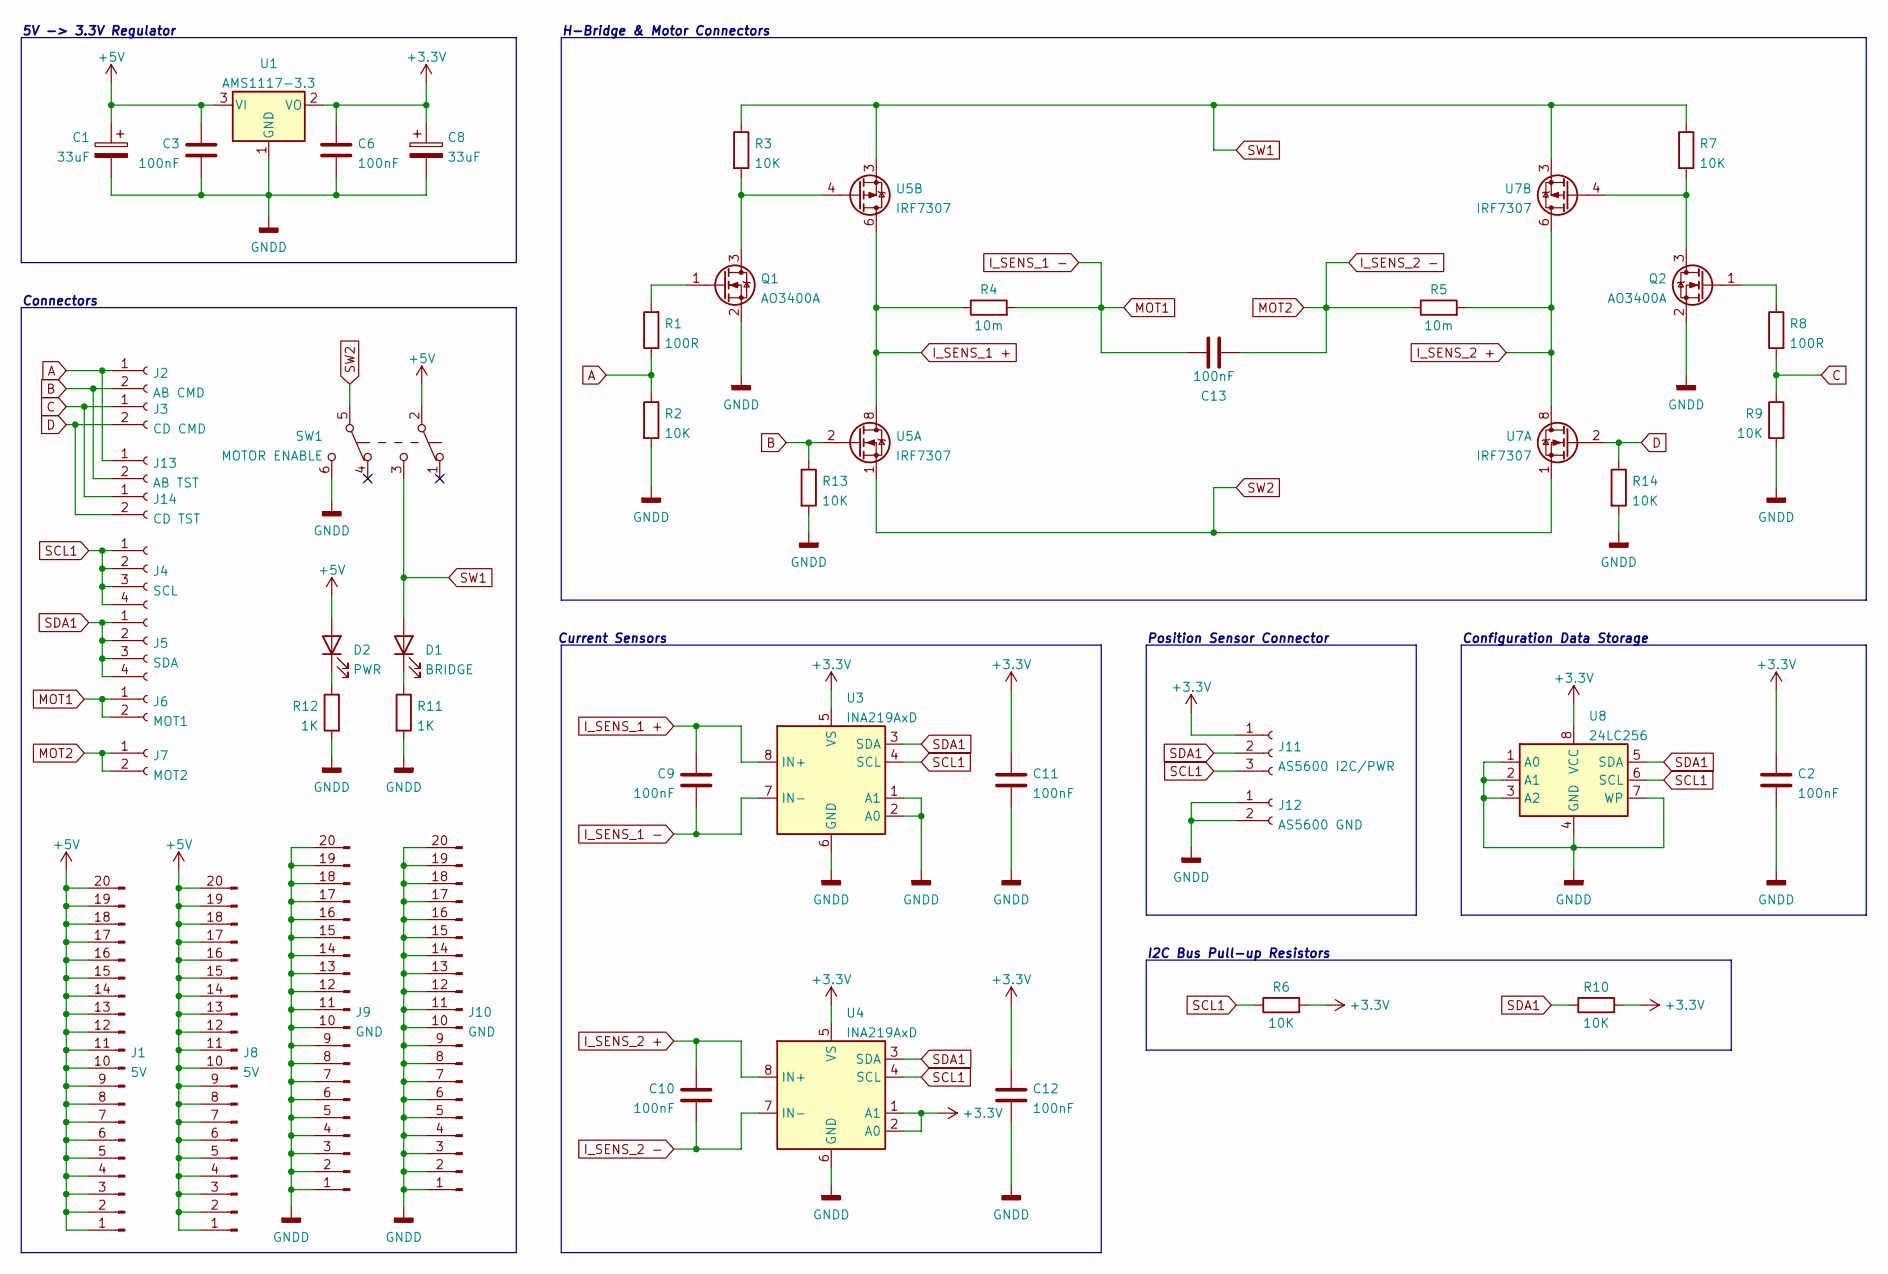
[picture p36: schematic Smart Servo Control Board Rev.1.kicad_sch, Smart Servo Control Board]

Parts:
C1, C8: 33uF; CP_Radial_D5.0mm_P2.50mm
C2, C3, C6, C9, C10, C11, C12, C13: 100nF; C_Disc_P2.54mm
D1: BRIDGE; D_1206_3216Metric_Pad1.42x1.75mm_HandSolder
D2: PWR; D_1206_3216Metric_Pad1.42x1.75mm_HandSolder
J1, J8: 5V; PinHeader_1x20_P2.54mm_Vertical
J2: AB CMD; PinHeader_1x02_P2.54mm_Vertical
J3: CD CMD; PinHeader_1x02_P2.54mm_Vertical
J4: SCL; PinHeader_1x04_P2.54mm_Vertical
J5: SDA; PinHeader_1x04_P2.54mm_Vertical
J6: MOT1; PinHeader_1x02_P2.54mm_Vertical
J7: MOT2; PinHeader_1x02_P2.54mm_Vertical
J9, J10: GND; PinHeader_1x20_P2.54mm_Vertical
J11: AS5600 I2C/PWR; PinHeader_1x03_P2.54mm_Vertical
J12: AS5600 GND; PinHeader_1x02_P2.54mm_Vertical
J13: AB TST; PinHeader_1x02_P2.54mm_Vertical
J14: CD TST; PinHeader_1x02_P2.54mm_Vertical
Q1, Q2: AO3400A; SOT-23 Breadboard Adapter
R1, R8: 100R; R_0603_1608Metric_Pad0.98x0.95mm_HandSolder
R2, R3, R6, R7, R9, R10, R13, R14: 10K; R_1206_3216Metric_Pad1.30x1.75mm_HandSolder
R4, R5: 10m; R_0603_1608Metric_Pad0.98x0.95mm_HandSolder
R11, R12: 1K; R_1206_3216Metric_Pad1.30x1.75mm_HandSolder
SW1: MOTOR ENABLE; DPDT Pushbutton
U1: AMS1117-3.3; SOT-223-3_TabPin2
U3, U4: INA219AxD; SOIC-8 Breadboard Adapter
U5, U7: IRF7307; SOIC-8 Breadboard Adapter
U8: 24LC256; SOIC-8 Breadboard Adapter

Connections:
+3V3: C2.2, C6.1, C8.1, C11.2, C12.2, J11.1, R6.2, R10.2, U1.2 (VO), U3.5 (VS), U4.1 (A1), U4.2 (A0), U4.5 (VS), U8.8 (VCC)
+5V: C1.1, C3.1, D2.2 (A), J1.1, J1.2, J1.3, J1.4, J1.5, J1.6, J1.7, J1.8, J1.9, J1.10, J1.11, J1.12, J1.13, J1.14, J1.15, J1.16, J1.17, J1.18, J1.19, J1.20, J8.1, J8.2, J8.3, J8.4, J8.5, J8.6, J8.7, J8.8, J8.9, J8.10, J8.11, J8.12, J8.13, J8.14, J8.15, J8.16, J8.17, J8.18, J8.19, J8.20, SW1.2 (B), U1.3 (VI)
A: J2.1, J13.1, R1.1, R2.1
B: J2.2, J13.2, R13.1, U5.2
C: J3.1, J14.1, R8.2, R9.1
D: J3.2, J14.2, R14.1, U7.2
GNDD: C1.2, C2.1, C3.2, C6.2, C8.2, C11.1, C12.1, J9.1, J9.2, J9.3, J9.4, J9.5, J9.6, J9.7, J9.8, J9.9, J9.10, J9.11, J9.12, J9.13, J9.14, J9.15, J9.16, J9.17, J9.18, J9.19, J9.20, J10.1, J10.2, J10.3, J10.4, J10.5, J10.6, J10.7, J10.8, J10.9, J10.10, J10.11, J10.12, J10.13, J10.14, J10.15, J10.16, J10.17, J10.18, J10.19, J10.20, J12.1, J12.2, Q1.2 (S), Q2.2 (S), R2.2, R9.2, R11.2, R12.2, R13.2, R14.2, SW1.6 (C), U1.1 (GND), U3.1 (A1), U3.2 (A0), U3.6 (GND), U4.6 (GND), U8.1 (A0), U8.2 (A1), U8.3 (A2), U8.4 (GND), U8.7 (WP)
I_SENS_1 +: C9.1, R4.1, U3.8 (IN+), U5.5, U5.6, U5.7, U5.8
I_SENS_1 -: C9.2, C13.1, J6.1, J6.2, R4.2, U3.7 (IN-)
I_SENS_2 +: C10.1, R5.2, U4.8 (IN+), U7.5, U7.6, U7.7, U7.8
I_SENS_2 -: C10.2, C13.2, J7.1, J7.2, R5.1, U4.7 (IN-)
unnamed: D1.1 (K), R11.1
unnamed: D2.1 (K), R12.1
unnamed: Q1.1 (G), R1.2
unnamed: Q1.3 (D), R3.2, U5.4
unnamed: Q2.1 (G), R8.1
unnamed: Q2.3 (D), R7.2, U7.4
SCL1: J4.1, J4.2, J4.3, J4.4, J11.3, R6.1, U3.4 (SCL), U4.4 (SCL), U8.6 (SCL)
SDA1: J5.1, J5.2, J5.3, J5.4, J11.2, R10.1, U3.3 (SDA), U4.3 (SDA), U8.5 (SDA)
SW1: D1.2 (A), R3.1, R7.1, SW1.3 (C), U5.3, U7.3
SW2: SW1.5 (B), U5.1, U7.1

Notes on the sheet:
Configuration Data Storage
Position Sensor Connector
I2C Bus Pull-up Resistors
H-Bridge & Motor Connectors
5V -> 3.3V Regulator
Current Sensors
Connectors

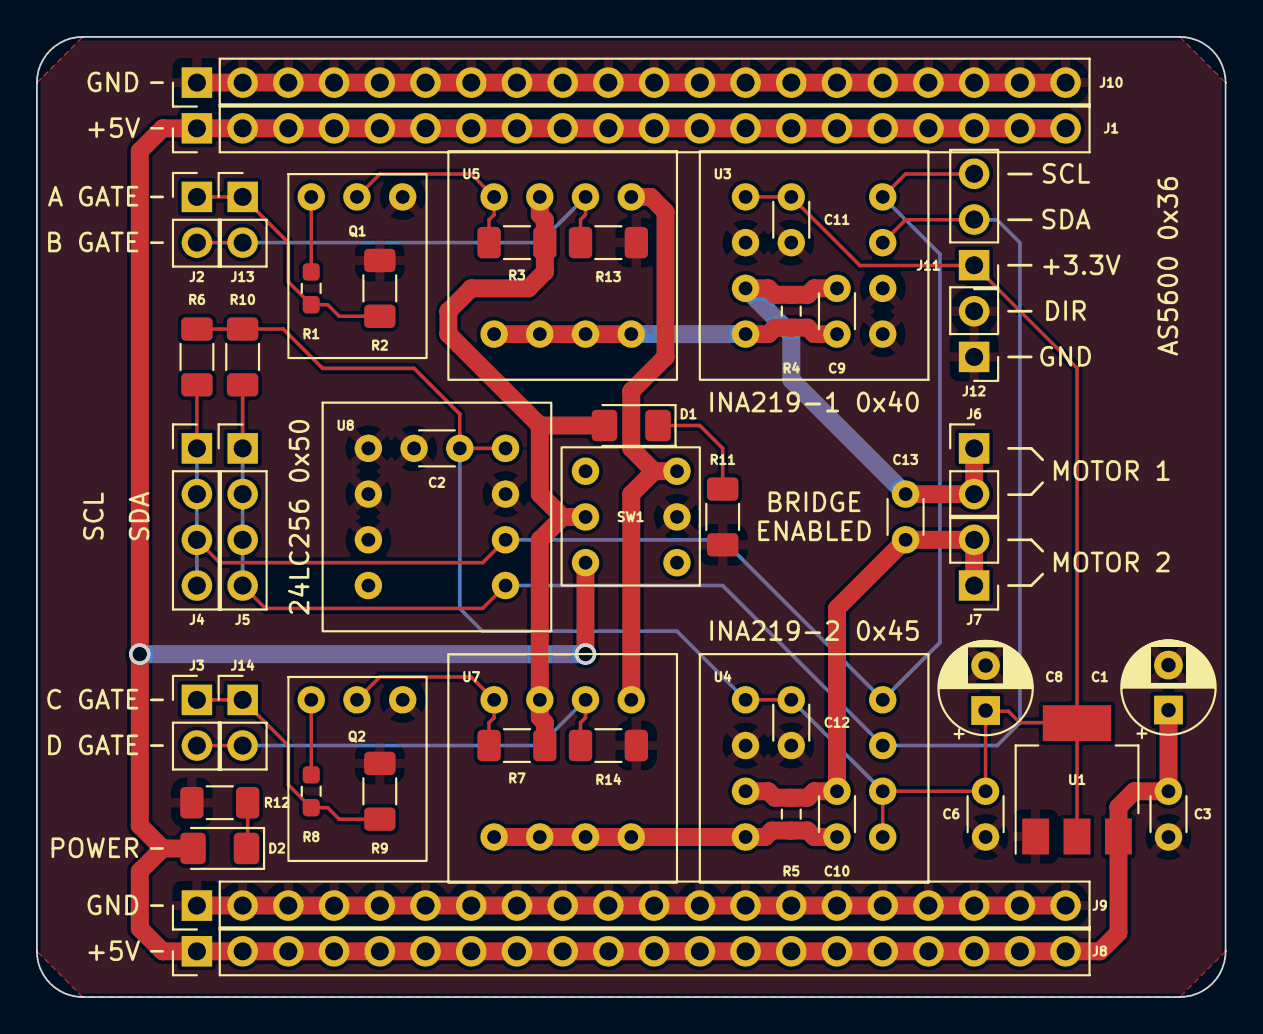
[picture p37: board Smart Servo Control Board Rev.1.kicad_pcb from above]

Board: 2 copper layers, 66.0 x 53.3 mm, 49 parts (0 on the bottom side), 21 nets.

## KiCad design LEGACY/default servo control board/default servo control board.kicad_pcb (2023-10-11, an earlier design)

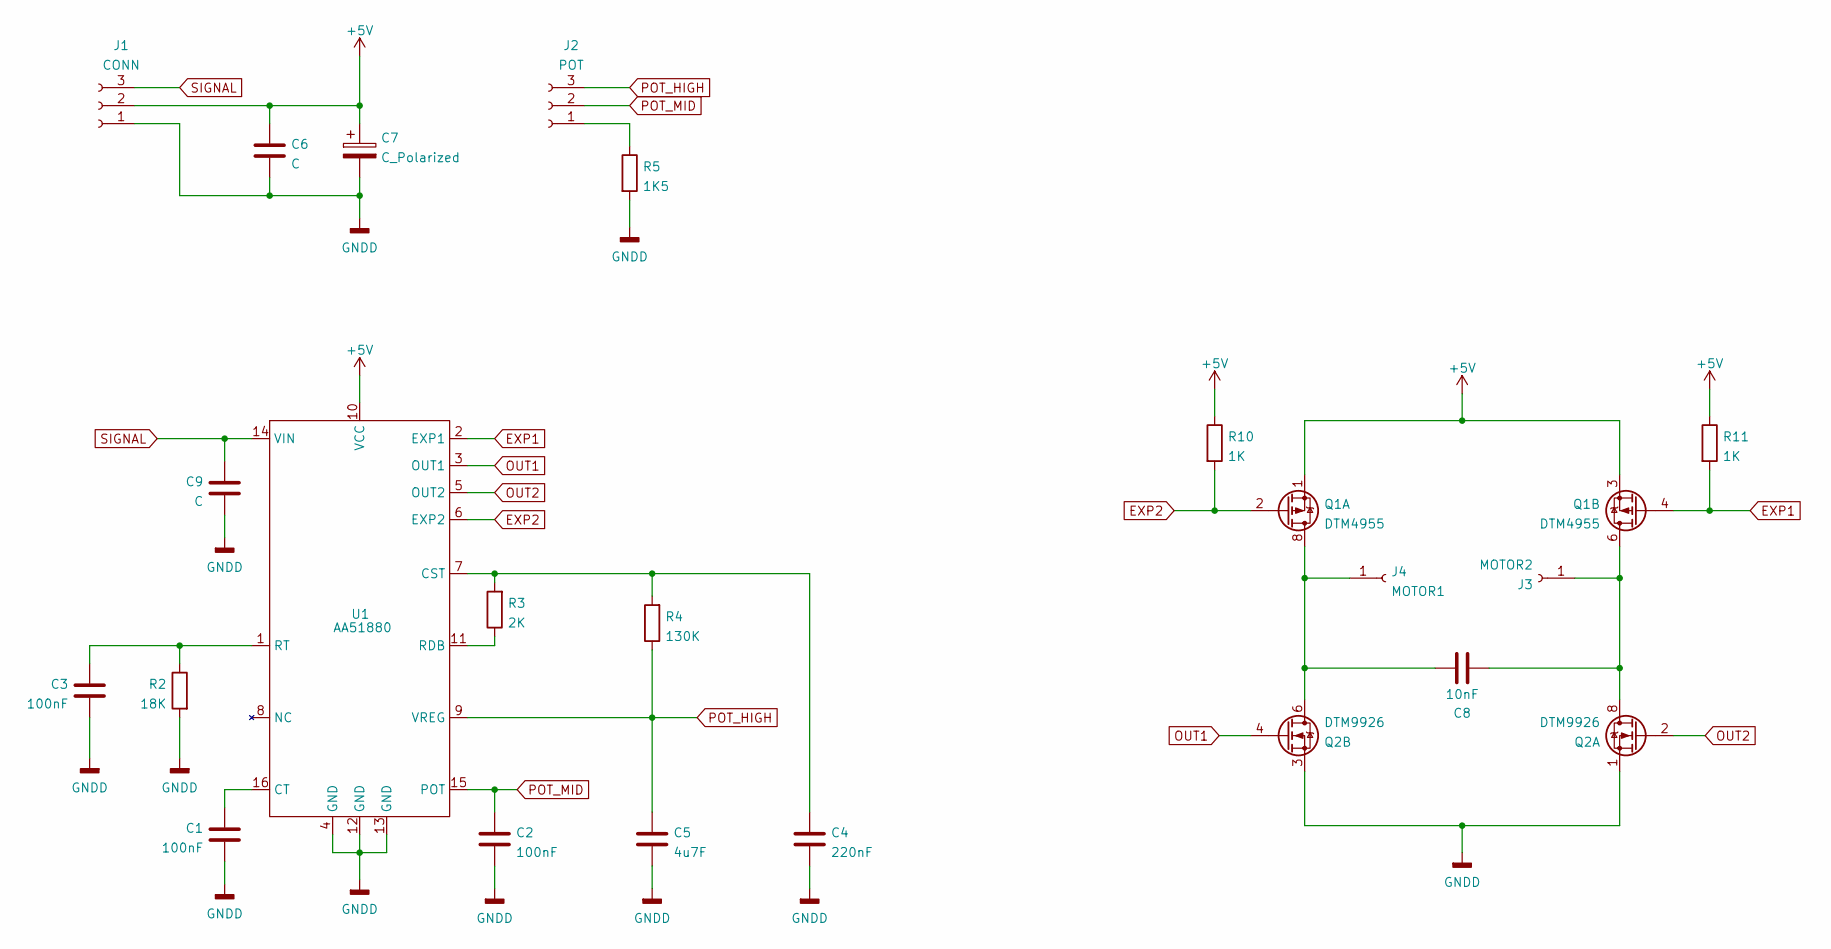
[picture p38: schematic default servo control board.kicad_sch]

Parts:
C1, C2, C3: 100nF; C_0402_1005Metric
C4: 220nF; C_0402_1005Metric
C5: 4u7F; C_0402_1005Metric
C6, C9: C; C_0402_1005Metric
C7: C_Polarized; C_1206_3216Metric
C8: 10nF; C_0402_1005Metric
J1: CONN; surface connector 1x3
J2: POT; PinSocket_1x03_P2.54mm_Vertical
J3: MOTOR2; PinSocket_1x01_P2.54mm_Vertical
J4: MOTOR1; PinSocket_1x01_P2.54mm_Vertical
Q1: DTM4955; SOIC-8_3.9x4.9mm_P1.27mm
Q2: DTM9926; SOIC-8_3.9x4.9mm_P1.27mm
R2: 18K; R_0402_1005Metric
R3: 2K; R_0402_1005Metric
R4: 130K; R_0402_1005Metric
R5: 1K5; R_0402_1005Metric
R10, R11: 1K; R_0402_1005Metric
U1: AA51880; SSOP-16_3.9x4.9mm_P0.635mm

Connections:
+5V: C6.1, C7.1, J1.2, Q1.1 (S1), Q1.3 (S2), R10.1, R11.1, U1.10 (VCC)
EXP1: Q1.4 (G2), R11.2, U1.2 (EXP1)
EXP2: Q1.2 (G1), R10.2, U1.6 (EXP2)
GNDD: C1.1, C2.2, C3.2, C4.2, C5.2, C6.2, C7.2, C9.2, J1.1, Q2.1 (S1), Q2.3 (S2), R2.2, R5.2, U1.4 (GND), U1.12 (GND), U1.13 (GND)
unnamed: C1.2, U1.16 (CT)
unnamed: C3.1, R2.1, U1.1 (RT)
unnamed: C4.1, R3.2, R4.2, U1.7 (CST)
unnamed: C8.1, J4.1, Q1.7 (D1), Q1.8 (D1), Q2.5 (D2), Q2.6 (D2)
unnamed: J2.1, R5.1
unnamed: C8.2, J3.1, Q1.5 (D2), Q1.6 (D2), Q2.7 (D1), Q2.8 (D1)
unnamed: R3.1, U1.11 (RDB)
OUT1: Q2.4 (G2), U1.3 (OUT1)
OUT2: Q2.2 (G1), U1.5 (OUT2)
POT_HIGH: C5.1, J2.3, R4.1, U1.9 (VREG)
POT_MID: C2.1, J2.2, U1.15 (POT)
SIGNAL: C9.1, J1.3, U1.14 (VIN)

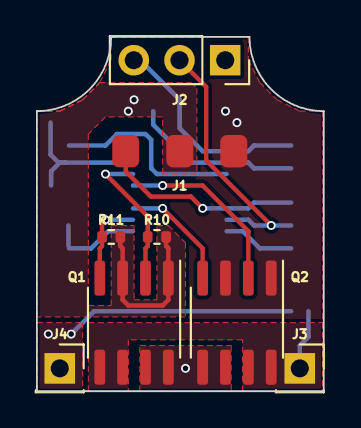
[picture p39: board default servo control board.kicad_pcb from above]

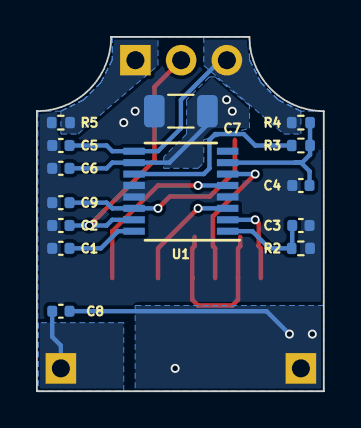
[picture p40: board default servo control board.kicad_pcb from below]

Board: 2 copper layers, 15.9 x 19.7 mm, 22 parts (14 on the bottom side), 16 nets.

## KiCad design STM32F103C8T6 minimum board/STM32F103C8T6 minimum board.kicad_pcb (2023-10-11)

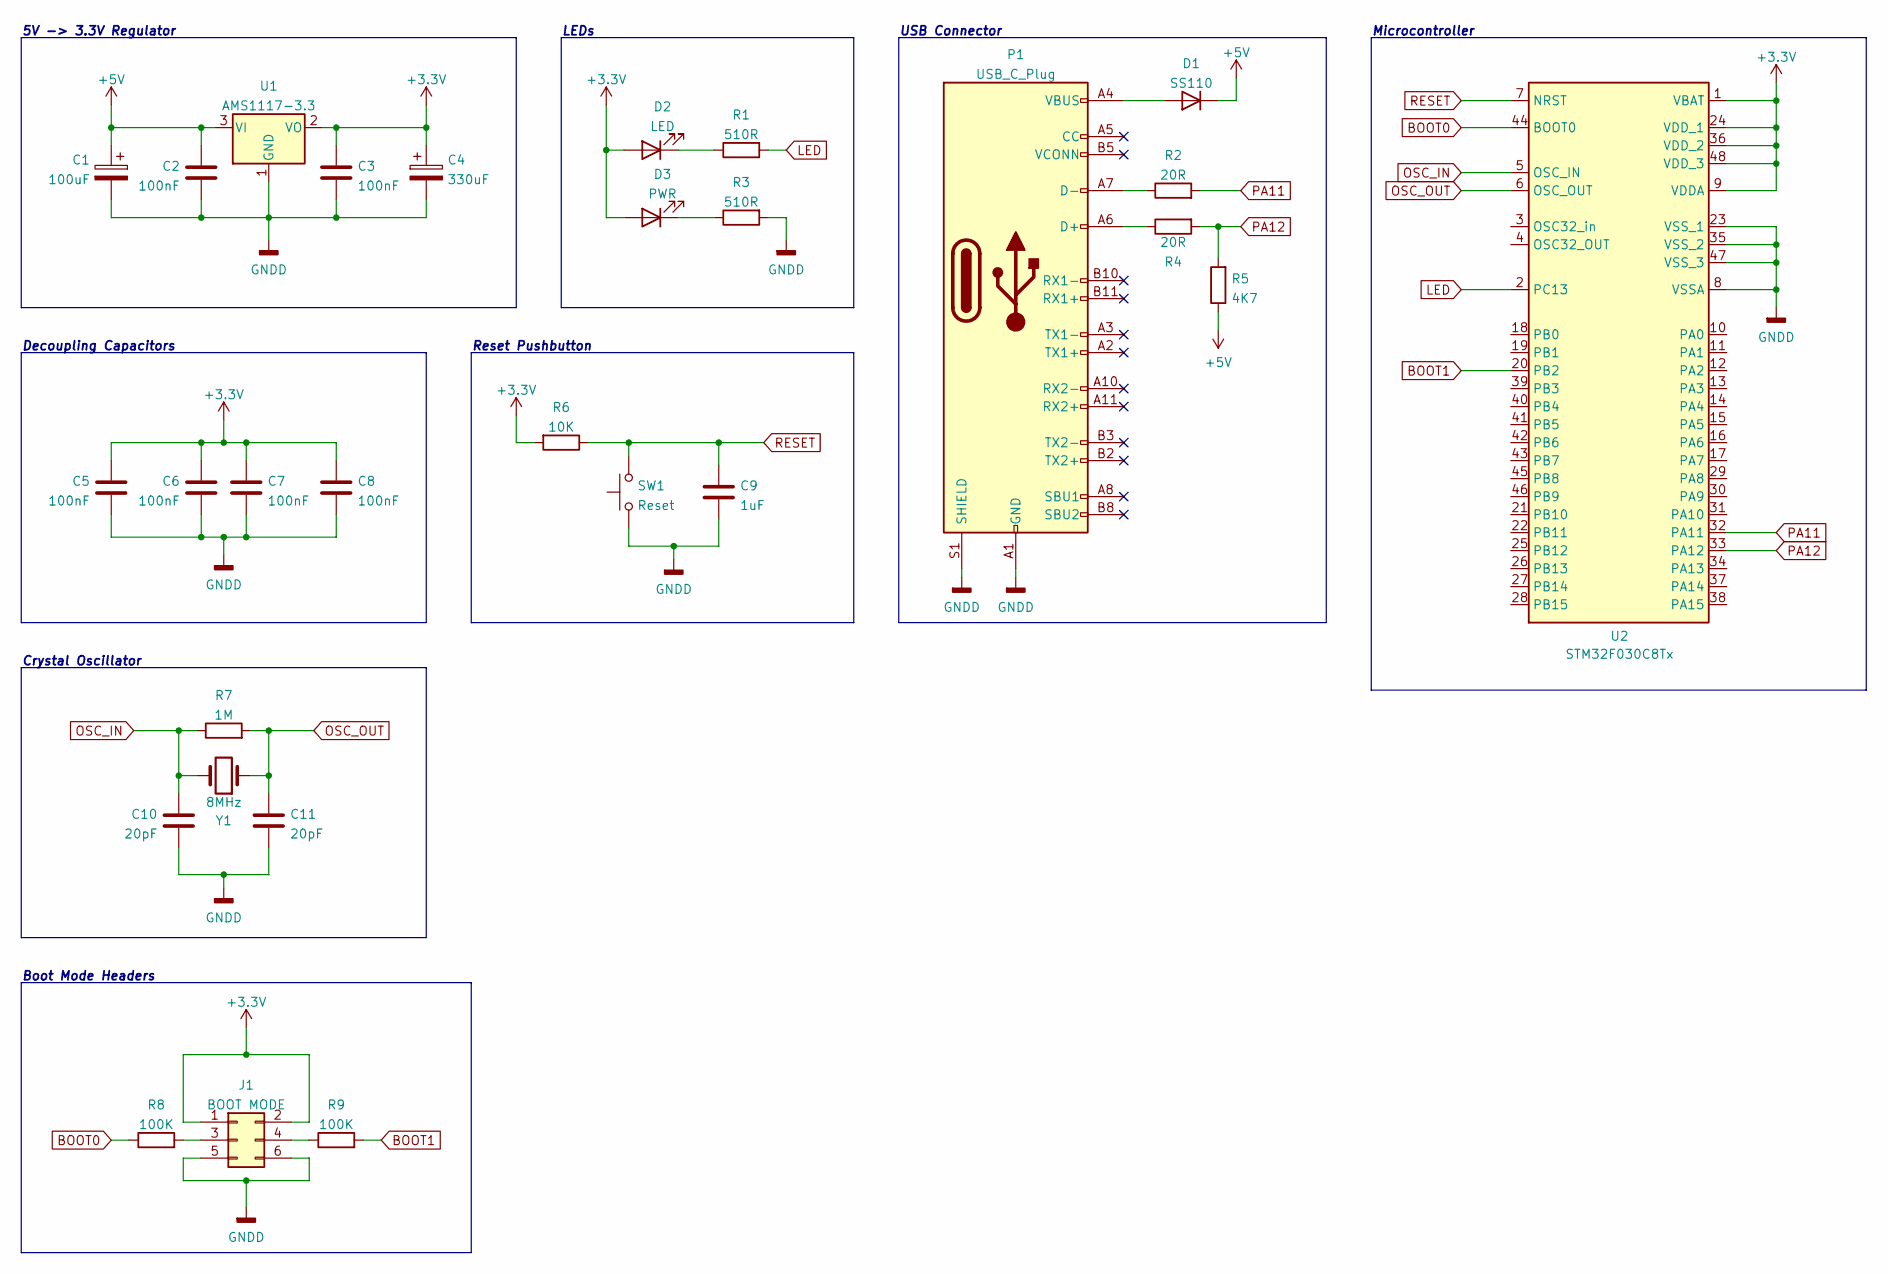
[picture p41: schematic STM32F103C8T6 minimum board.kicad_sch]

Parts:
C1: 100uF; C_0603_1608Metric
C2, C3, C5, C6, C7, C8: 100nF; C_0603_1608Metric
C4: 330uF; C_0603_1608Metric
C9: 1uF; C_0603_1608Metric
C10, C11: 20pF; C_0603_1608Metric
D1: SS110; D_SMA
D2: LED; D_0201_0603Metric
D3: PWR; D_0201_0603Metric
J1: BOOT MODE; PinHeader_2x03_P2.54mm_Vertical_SMD
P1: USB_C_Plug; USB_C_Receptacle_HRO_TYPE-C-31-M-12
R1, R3: 510R; R_0603_1608Metric
R2, R4: 20R; R_0603_1608Metric
R5: 4K7; R_0603_1608Metric
R6: 10K; R_0603_1608Metric
R7: 1M; R_0603_1608Metric
R8, R9: 100K; R_0603_1608Metric
SW1: Reset; SW_SPST_B3U-1000P
U1: AMS1117-3.3; SOT-223-3_TabPin2
U2: STM32F030C8Tx; LQFP-48_7x7mm_P0.5mm
Y1: 8MHz; Crystal_SMD_5032-2Pin_5.0x3.2mm

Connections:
+3V3: C3.1, C4.1, C5.1, C6.1, C7.1, C8.1, D2.2 (A), D3.2 (A), J1.1, J1.2, R6.2, U1.2 (VO), U2.1 (VBAT), U2.9 (VDDA), U2.24 (VDD_1), U2.36 (VDD_2), U2.48 (VDD_3)
+5V: C1.1, C2.1, D1.2 (K), R5.1, U1.3 (VI)
BOOT0: R8.1, U2.44 (BOOT0)
BOOT1: R9.2, U2.20 (PB2)
GNDD: C1.2, C2.2, C3.2, C4.2, C5.2, C6.2, C7.2, C8.2, C9.2, C10.2, C11.2, J1.5, J1.6, P1.A1 (GND), P1.A12 (GND), P1.B1 (GND), P1.B12 (GND), P1.S1 (SHIELD), R3.2, SW1.1, U1.1 (GND), U2.8 (VSSA), U2.23 (VSS_1), U2.35 (VSS_2), U2.47 (VSS_3)
LED: R1.2, U2.2 (PC13)
unnamed: D1.1 (A), P1.A4 (VBUS), P1.A9 (VBUS), P1.B4 (VBUS), P1.B9 (VBUS)
unnamed: D2.1 (K), R1.1
unnamed: D3.1 (K), R3.1
unnamed: J1.3, R8.2
unnamed: J1.4, R9.1
unnamed: P1.A6 (D+), R4.1
unnamed: P1.A7 (D-), R2.1
OSC_IN: C10.1, R7.1, U2.5 (OSC_IN), Y1.2
OSC_OUT: C11.1, R7.2, U2.6 (OSC_OUT), Y1.1
PA11: R2.2, U2.32 (PA11)
PA12: R4.2, R5.2, U2.33 (PA12)
RESET: C9.1, R6.1, SW1.2, U2.7 (NRST)

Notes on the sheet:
LEDs
USB Connector
Crystal Oscillator
Microcontroller
Decoupling Capacitors
Reset Pushbutton
Boot Mode Headers
5V -> 3.3V Regulator

Board: 2 copper layers, 29 parts (0 on the bottom side), 18 nets, no tracks yet.

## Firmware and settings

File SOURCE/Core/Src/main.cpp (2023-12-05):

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
/* Includes ------------------------------------------------------------------*/
#include "main.h"

/* USER CODE BEGIN Includes */
#include "AS5600.hpp"
#include "INA219.hpp"
/* USER CODE END Includes */

I2C_HandleTypeDef hi2c1;

TIM_HandleTypeDef htim1;

void SystemClock_Config(void);
static void MX_GPIO_Init(void);
static void MX_TIM1_Init(void);
static void MX_I2C1_Init(void);
/* USER CODE BEGIN PFP */

float i1 = 0, i2 = 0, i = 0;

float v_bus1 = 0, v_bus2 = 0, v = 0;

float angle = 0;

/* USER CODE END PFP */

/**
  * @brief  The application entry point.
  * @retval int
  */
int main(void)
{
  /* USER CODE BEGIN 1 */
	AS5600 Encoder(&hi2c1, 0x36, AS5600::CLOCK_WISE, 0x01);

	const float shunt_resistor = 0.1, max_expected_current = 3.0;	// Ohms, Amps
	INA219 CurrentSensor1(&hi2c1, max_expected_current, shunt_resistor, 0x40, 0x01);
	INA219 CurrentSensor2(&hi2c1, max_expected_current, shunt_resistor, 0x44, 0x01);

  /* USER CODE END 1 */

  /* MCU Configuration--------------------------------------------------------*/

  /* Reset of all peripherals, Initializes the Flash interface and the Systick. */
  HAL_Init();

  /* Configure the system clock */
  SystemClock_Config();

  /* Initialize all configured peripherals */
  MX_GPIO_Init();
  MX_TIM1_Init();
  MX_I2C1_Init();
  /* Infinite loop */
  /* USER CODE BEGIN WHILE */
  while (1)
  {
    /* USER CODE END WHILE */


	bool connected = CurrentSensor1.isConnected();
	connected = CurrentSensor2.isConnected();

	i1 = CurrentSensor1.getCurrent_A();
	i2 = CurrentSensor2.getCurrent_A();
	i = (i1 - i2) / 2;

	v_bus1 = CurrentSensor1.getBusVoltage_V();
	v_bus2 = CurrentSensor2.getBusVoltage_V();
	v = (v_bus2 - v_bus1);

	angle = Encoder.getRealAngle(AS5600::DEGREES);

	HAL_Delay(1);

    /* USER CODE BEGIN 3 */
  }
  /* USER CODE END 3 */
}

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
/* USER CODE BEGIN 4 */
int _write(int file, char *ptr, int len)
{
  (void)file;
  int DataIdx;

  for (DataIdx = 0; DataIdx < len; DataIdx++)
  {
    ITM_SendChar(*ptr++);
  }
  return len;
}
/* USER CODE END 4 */
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


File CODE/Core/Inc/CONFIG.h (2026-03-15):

/*
 * CONFIG.h
 *
 *  File containing all the system parameters and configuration data.
 *
 */

#pragma once

#include "stm32f1xx_hal.h"

#include "DRV8870.hpp"
#include "AS5600.hpp"
#include "control.hpp"
#include "i2c_slave.hpp"


namespace RegAddr {
	// SW-PID Controller
	constexpr uint8_t ProportionalGain 		= 0x00;
	constexpr uint8_t IntegralGain 			= 0x01;
	constexpr uint8_t DerivativeGain 		= 0x02;
	constexpr uint8_t AntiwindupMax 		= 0x03;
	constexpr uint8_t AntiwindupMin			= 0x04;
	constexpr uint8_t OutputMax 			= 0x05;
	constexpr uint8_t OutputMin 			= 0x06;

	// Servo Motor State
	constexpr uint8_t DesiredPosition 		= 0x20;
	constexpr uint8_t ActualPosition 		= 0x21;
	constexpr uint8_t PositionOffset		= 0x22;
	constexpr uint8_t MotorCurrent	 		= 0x23;
	constexpr uint8_t MotorVoltage 			= 0x24;
	constexpr uint8_t MotorPower 			= 0x25;
	constexpr uint8_t DutyCycle 			= 0x26;

	// AS5600 Position Sensor
	constexpr uint8_t ZeroPosition 			= 0x40;
	constexpr uint8_t StopPosition 			= 0x41;

	// INA219 Current Sensor
	constexpr uint8_t CurrentCalibration 	= 0x42;

	// Slave Configuraiton
	constexpr uint8_t DeviceAddress 		= 0xF0;
	constexpr uint8_t DeviceConfiguration 	= 0xFF;
}

namespace DefaultSettings {
	// SW-PID Controller
	constexpr float TimeStep 				= 1e-3f;
	constexpr float ProportionalGain 		= 10.0f;
	constexpr float IntegralGain 			= 0.9f;
	constexpr float DerivativeGain 			= 0.1f;
	constexpr float AntiwindupMax			= 5.0f;
	constexpr float AntiwindupMin			= -5.0f;
	constexpr float OutputMax 				= 1.0f;
	constexpr float OutputMin 				= -1.0f;

	// DRV8870 Driver
	constexpr uint16_t DRV8870_Steps 		= 1024;
	constexpr uint32_t DRV8870_IN1			= TIM_CHANNEL_1;
	constexpr uint32_t DRV8870_IN2			= TIM_CHANNEL_2;

	// General I2C
	constexpr uint32_t I2C_MaxDelay			= 1;

	// AS5600 Position Sensor
	constexpr uint8_t AS5600_Address 		= 0x36;
	constexpr uint16_t AS5600_ZeroPos 		= 0x000;
	constexpr uint16_t AS5600_StopPos 		= 0xFFF;
	constexpr int32_t AS5600_Offset			= -2048;

	// INA219 Current Sensor
	constexpr uint8_t INA219_Address 		= 0x40;
	constexpr uint16_t INA219_Calibration 	= 0x0000;

	// Slave Configuration
	constexpr uint8_t SlaveAddress			= 0x52;
}

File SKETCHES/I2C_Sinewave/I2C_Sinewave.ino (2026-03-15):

#include <Wire.h>
#include <math.h>

// --- Indirizzi I2C degli slave ---
#define I2C_ADDR_1  0x50
#define I2C_ADDR_2  0x51
#define I2C_ADDR_3  0x52
#define REG_WRITE   0x20

const unsigned long period = 10;  // 10 ms
unsigned long lastTime = 0;

// Parametri della sinusoide
const float freq = M_PI / 5.0;    // frequenza angolare
const float Ts = 0.01;            // 10 ms
const float amplitude = 4065.0 / 2.0;
const float offset = 4065.0 / 2.0;

float t = 0.0;

// --- Pin I2C hardware (per ATmega2560: SDA=20, SCL=21)
const uint8_t PIN_SDA = 20;
const uint8_t PIN_SCL = 21;

// 🔧 Funzione per reset hardware del bus I2C
void resetI2CBus() {
  Serial.println("🔄 Reset hardware I2C...");

  Wire.end();

  pinMode(PIN_SCL, OUTPUT);
  pinMode(PIN_SDA, INPUT_PULLUP);

  // 1. Genera fino a 9 clock su SCL per liberare SDA
  for (int i = 0; i < 9; i++) {
    if (digitalRead(PIN_SDA) == HIGH) break;
    digitalWrite(PIN_SCL, HIGH);
    delayMicroseconds(5);
    digitalWrite(PIN_SCL, LOW);
    delayMicroseconds(5);
  }

  // 2. Forza condizione di STOP
  pinMode(PIN_SDA, OUTPUT);
  digitalWrite(PIN_SDA, LOW);
  delayMicroseconds(5);
  digitalWrite(PIN_SCL, HIGH);
  delayMicroseconds(5);
  digitalWrite(PIN_SDA, HIGH);
  delayMicroseconds(5);

  // 3. Ripristina bus
  Wire.begin();
  Wire.setClock(400000);

  Serial.println("✅ Bus I2C resettato");
}

// --- Scrittura con timeout e reset hardware se necessario
bool writeI2CwithTimeout(uint8_t addr, uint8_t reg, uint16_t value) {
  uint8_t low = value & 0xFF;
  uint8_t high = (value >> 8) & 0xFF;

  unsigned long start = micros();

  Wire.beginTransmission(addr);
  Wire.write(reg);
  Wire.write(low);
  Wire.write(high);
  byte error = Wire.endTransmission();

  if ((micros() - start > 1000UL) || error != 0) {
    Serial.print("⚠️ Errore/timeout I2C (codice ");
    Serial.print(error);
    Serial.print(") su device 0x");
    Serial.println(addr, HEX);

    resetI2CBus();  // reset fisico

    // Ritento una sola volta
    Wire.beginTransmission(addr);
    Wire.write(reg);
    Wire.write(low);
    Wire.write(high);
    error = Wire.endTransmission();

    if (error == 0) {
      Serial.println("✅ Retry riuscito");
      return true;
    } else {
      Serial.print("❌ Fallimento dopo retry su 0x");
      Serial.print(addr, HEX);
      Serial.print(" (errore ");
      Serial.print(error);
      Serial.println(")");
      return false;
    }
  }

  return true;
}

void setup() {
  Serial.begin(115200);
  Wire.begin();
  Wire.setClock(100000);
  Serial.println("✅ Generatore sinusoidale I2C per 3 dispositivi avviato");
}

void loop() {
  unsigned long now = millis();
  if (now - lastTime >= period) {
    lastTime = now;

    // Calcolo sinusoide
    float val_f = offset + amplitude * sin(freq * t);
    uint16_t val = (uint16_t) round(val_f);

    // Scrive su tutti i dispositivi
    bool ok1 = writeI2CwithTimeout(I2C_ADDR_1, REG_WRITE, val);
    bool ok2 = writeI2CwithTimeout(I2C_ADDR_2, REG_WRITE, val);
    bool ok3 = writeI2CwithTimeout(I2C_ADDR_3, REG_WRITE, val);

    if (ok1 && ok2 && ok3) {
      Serial.print("I2C -> 0x");
      Serial.print(I2C_ADDR_1, HEX);
      Serial.print(", 0x");
      Serial.print(I2C_ADDR_2, HEX);
      Serial.print(", 0x");
      Serial.print(I2C_ADDR_3, HEX);
      Serial.print(" [0x");
      Serial.print(REG_WRITE, HEX);
      Serial.print("] = ");
      Serial.println(val);
    }

    t += Ts;
  }
}

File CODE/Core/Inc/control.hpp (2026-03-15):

/*
 * control.hpp
 *
 *  Module containing classes and function for system control.
 *
 */

#pragma once

#include <algorithm>
#include <cstdint>
#include <cmath>


namespace mth {
	constexpr float PI = 3.14159265358979323846f;

	template<class T>
    constexpr T clamp(const T& v, const T& lo, const T& hi) {
        return (v < lo) ? lo : (hi < v) ? hi : v;
    }

	// Symmetric overload
    template<class T>
    constexpr T clamp(const T& v, const T& th) {
        return clamp(v, -th, th);
    }


	template<class T>
	constexpr T deadzone(const T& v, const T& lo, const T& hi) {
		return v - clamp(v, lo, hi);
	}

	// Symmetric overload
    template<class T>
    constexpr T deadzone(const T& v, const T& th) {
        return deadzone(v, -th, th);
    }


	template<class T>
	constexpr int sign(const T& v) {
		return (T(0) < v) - (v < T(0));
	}


    template<class T>
    constexpr T abs(T v) {
        return (v < T(0)) ? -v : v;
    }
}


class DiscreteBlock {
public:
	virtual ~DiscreteBlock() = default;

	virtual float step(float input) = 0;
	virtual void reset(float value = 0.0f) = 0;
};


class DiscreteDelay : public DiscreteBlock {
public:

	DiscreteDelay() : _prev_input(0.0f) {}

	float step(float input) override {
		float output = _prev_input;
		_prev_input = input;
		return output;
	}

	float state() { return _prev_input; }

	void reset(float value = 0.0f) override { _prev_input = value; }


protected:
	float _prev_input;
};


class DiscreteIntegrator : public DiscreteBlock {
public:

	DiscreteIntegrator(float Ts, float min_out = -1e6f, float max_out = 1e6f, float K = 1.0f)
		: _Ts(Ts), _min_out(min_out), _max_out(max_out), _K(K),
		  _delay(), _first_step(true), _first_value(0.0f) {}

	float step(float input) override {
		if (_first_step) {
			_delay.reset(_first_value);
			_first_step = false;
		}

		float prev = _delay.state();

		float state = prev + _K * _Ts * input;
		state = mth::clamp(state, _min_out, _max_out);

		_delay.step(state);

		return state;
	}

	float state() { return mth::clamp(_delay.state(), _min_out, _max_out); }

	void reset(float value = 0.0f) override { _first_step = true; _first_value = value; }


protected:
	float _Ts;
	float _min_out, _max_out;
	float _K;
	DiscreteDelay _delay;
	bool _first_step;
	float _first_value;
};


class DiscreteDerivative : public DiscreteBlock {
public:

	DiscreteDerivative(float Ts, float K = 1.0f)
		: _Ts(Ts), _K(K), _delay(), _first_step(true) {}

	float step(float input) override {
		if (_first_step) {
			_delay.reset(input);
			_first_step = false;

			// No derivative for first step
			return 0.0f;
		}

		float prev = _delay.step(input);

		float output = _K * (input - prev) / _Ts;
		return output;
	}

	void reset(float value = 0.0f) override { _first_step = true; }


protected:
	float _Ts, _K;
	DiscreteDelay _delay;
	bool _first_step;
};


class GlitchFilter : public DiscreteBlock {
public:

	GlitchFilter(float max_delta)
		: _max_delta(max_delta), _delay(), _first_step(true) {}

	float step(float input) override {
		// First Step: initialize the delay
		if(_first_step){
			_delay.reset(input);
			_first_step = false;
			return input;
		}

		// Get previous value from delay
		float prev = _delay.step(input);
		float delta = input - prev;

		float output = input;

		// If a glitch is detected use previous value
		if (std::fabs(delta) >= _max_delta) {
			output = prev;
		}

		return output;
	}

	void reset(float value = 0.0f) override { _first_step = true; }


protected:
	float _max_delta;
	DiscreteDelay _delay;
	bool _first_step;
};


class DiscreteFilter : public DiscreteBlock {
public:

	DiscreteFilter(float a1, float a0, float b1, float b0)
		: _a1(a1), _a0(a0), _b1(b1), _b0(b0),
		  _input_delay(), _output_delay(), _first_step(true) {}

	float step(float input) override {
		if (_first_step) {
			_input_delay.reset(0.0f);
			_output_delay.reset(0.0f);
			_first_step = false;
		}

		// Previous input and output
		float in_prev = _input_delay.step(input);
		float out_prev = _output_delay.state();

		// New output
		float output = (_a1 * in_prev + _a0 * input - _b1 * out_prev) / _b0;
		_output_delay.step(output);

		return output;
	}

	float state() { return _output_delay.state(); }

	void reset(float value = 0.0f) override {
		_first_step = true;
	}


protected:
	float _a1, _a0;
	float _b1, _b0;

	DiscreteDelay _input_delay, _output_delay;

	bool _first_step;
};


class SwitchingPID {
public:

	SwitchingPID(float Ts, float Kp, float Ki, float Kd)
		: _Ts(Ts), _Kp(Kp), _Ki(Ki), _Kd(Kd),
		  _windup_min(-1e6f), _windup_max(1e6f),
		  _out_min(-1e6f), _out_max(1e6f),
		  _integrator(_Ts), _derivative(_Ts), _glitch_filter(100.0f),
		  _ref_filter(0.6f, -0.6f, 1e-3f, -4e-3f),
		  _switching_state(SystemState::StickSlip) {}

	float step(float reference, float feedback) {
		// Error calculation
		float error = reference - feedback;

		// Sigma and Phi
		float sigma = _Ki * error;
		float raw_phi = _Kp * (error + _integrator.state());
		float phi = mth::clamp(raw_phi, _windup_min, _windup_max);

		// Anti-windup
		bool cond_1 = mth::sign(sigma) == mth::sign(mth::deadzone(raw_phi, _windup_min, _windup_max));
		bool cond_2 = mth::deadzone(raw_phi, _windup_min, _windup_max) != 0;

		if (cond_1 && cond_2) {
			_integrator.step(0);
		}
		else {
			_integrator.step(sigma);
		}

		// Velocity
		float velocity = _glitch_filter.step(_derivative.step(feedback));

		// Switching logic
		if ((_switching_state == SystemState::StickSlip) && (sigma * phi <= 0)) {
			// Transition to Overshoot
			phi = -phi;
			_integrator.reset((phi / _Kp) - error);
			_switching_state = SystemState::Overshoot;
		}
		else if ((_switching_state == SystemState::Overshoot) && (velocity * phi >= 0)) {
			// Transition to StickSlip
			phi = _Kp * sigma / _Ki;
			_integrator.reset();
			_switching_state = SystemState::StickSlip;
		}
		// Otherwise keep previous state

		// Output calculation
		float command = mth::clamp(phi - _Kd * velocity, _out_min, _out_max);

		// Dead-banding if needed
		/*
		float ref_velocity = mth::clamp(mth::abs(_ref_filter.step(reference)), 1.0f);

		float th_velocity = 0.01; 			// param 1
		float LSB = 2 * mth::PI / 4096.0f;	// param 2
		uint8_t steps = 5;					// param 3

		if ((ref_velocity < th_velocity) && (mth::abs(error) < LSB * steps)) {
			command = 0.0f;
		}
		*/
		// Return command
		return command;
	}


	enum class ControllerParam : uint8_t {
		ProportionalGain,
		IntegralGain,
		DerivativeGain,

		AntiwindupMax,
		AntiwindupMin,

		OutputMax,
		OutputMin,
	};
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

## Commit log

2023-10-11 Initial push
    Push of the starting files
    [MG996R Manufacturer Data.xlsx, STM32F103C8T6 minimum board.kicad_pcb, STM32F103C8T6 minimum board.kicad_sch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]
2023-10-11 Modello Simulink
    Creato modello simulink iniziale del motore e del ponte H.
    Sono da stimare/misurare i valori del motore e da fare refactoring del modello simulink per un migliore layout.
2023-10-13 piccoli cambiamenti al modello simulink
    Provato a vedere la corrente del carico totale e del motore in condizioni normali, a pieno carico e di shoot-through
    by PippoGot
2023-10-13 Sistemato il modello simulink
    ho sistemato e riordinato il modello simulink. ho sostituito il modello del ponte H fatto a transistor con un blocco apposito, probabilmente ci sono impostazioni sbagliate sui mosfet da sistemare.
2023-10-19 Chiuso loop di controllo
    prima prova per l'anello di controllo, il controllore va progettato meglio, deve anche includere una soglia di errore nel quale non si attiva.
    risistemato il circuito del ponte H, non si possono rimuovere i MOSFET AO3400 a causa della differenza tra le tensioni di alimentazione del microcontrollore e del motore, però si può provare a usare le resistenze di pull-down del microcontrollore. rimane da risistemare lo schema del ponte per renderlo più ordinato
2023-10-23 Aggiunto file README
    Aggiunto file README per riassumere gli obiettivi del progetto e descrivere la struttura delle cartelle
2023-10-23 Aggiunti parametri e provato a progettare il controllore
    Il controllore da problemi e probabilmente è da riprogettare. Aggiunti i parametri del motore e dei MOSFET
    [MG996R Angle Sampling Data.xlsx]
2023-10-23 Aggiunta cartella per il codice
    creata la cartella in cui verrà messo tutto il codice per il microcontrollore
2023-10-23 Aggiunto file specifiche per il blocco PWM
    file per il comportamento del blocco PWM simulink
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2023-10-23 Creato modello del motore su simulink
    nuovo modello simulink puro del motore per confronto.
    modifica unità di misura su params motor.J
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2023-10-24 Testato collegamento simulink - ESP32
    riuscito il collegamento tra simulink e la scheda ESP32.
    aggiunti i file generati automaticamente da matlab al gitignore.
    rinominata la cartella per le simulazioni, gli spazi nel nome davano errore per il file si simulazione.
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2023-10-27 controllori
    Abbiamo cercato di risolvere overshoot di velocità e corrente - scarsi risultati
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2023-10-30 Controllore velocità
    Probabilmente il controllore per la velocità è stato calcolato bene, incluso anche il loop di corrente.
    cominciato il loop per la posizione
2023-10-31 Controllore sistemato
    il codice per i parametri del controllore funzionano, anche se rimane da capire come calcolare il Kp della posizione. risistemare blocchi controllore prima di fare merge
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2023-11-01 Connessi tutti i blocchi utili
    collegati controllore, interfaccia PWM, ponte H e motore assieme e testato il modello. funziona
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2023-11-08 Creato progetto stm32
    creato il file e la cartella di progetto stm32.
    testato il pwm con successo
2023-11-08 Risistemato codice parametri e modello simulink
    risistemato il modello simulink e il codice dei parametri.
    la simulazione è lenta e il funzionamento del controllore è da verificare.
2023-11-10 Cambiato blocco PWM
    ora la simulazione funziona in modo corretto. provare diversi tempi di campionamento e frequenze pwm, e aggiungere rumore.
2023-11-11 Aggiunto sensore di posizione
    quando il sistema arriva vicino alla reference oscilla in modo divergente, da sistemare, provare con il kalman filter
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2023-11-17 Implementate moduli e classi per interfaccia I2C
    implementato generica classe per la comunicazione via I2C.
    implementata sottoclasse per il sensore AS5600.
    compila ok, testate alcune funzioni, va testato completamente e documentato il codice in dettaglio.
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2023-11-22 iniziato board design
    [Smart Servo Control Board Rev.1.kicad_pcb, Smart Servo Control Board Rev.1.kicad_sch]
2023-11-22 salvataggio layout board
    tornare a questo salvataggio per riprovare.
    piani potenza interni e piani segnali esterni, da scambiare ?
    [Smart Servo Control Board Rev.1.kicad_pcb, Smart Servo Control Board Rev.1.kicad_sch]
2023-11-25 implementata libreria per sensore INA219
    implementata libreria per INA219.
    piccolo refactoring della libreria per AS5600 e I2C device.
    semplice test della lettura di corrente con esito positivo.
    rimane da documentare l'intero codice scritto.
    possibile modifica della libreria per implementare il sensore anche come sensore di tensione ?
2023-11-28 Acquisiti dati caratteristica servo
    acquisiti dati per la verifica del (mal)funzionamento dell'output del servomotore e tracciati grafici di caratteristica, errore e isteresi.
    [Old Servo Characteristic Data.xlsx]
2023-11-28 Aggiunte misure di un secondo servo
    [Old Servo Characteristic Data.xlsx]
2023-11-28 Test CubeMonitor
    testata app per l'acqusizione e visualizzazione di dati da scheda STM32
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2023-12-04 Prima versione definitiva PCB
    tracciate le piste nel modo migliore possibile per ora, resta da sistemare il silkscreen.
    [Smart Servo Control Board Rev.1.kicad_pcb, Smart Servo Control Board Rev.1.kicad_sch]
2024-12-03 Updated with new simulink model, moved legacy material
    [MG996R Angle Sampling Data.xlsx, Old Servo Characteristic Data.xlsx, STM32F103C8T6 minimum board.kicad_pcb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]
2024-12-10 hardware in loop model and rebase of git repo
    [MG996R Angle Sampling Data.xlsx]
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2025-03-04 lugre model and LQR controller, compensation looks like could work
    [MG996R Angle Sampling Data.xlsx, Smart Servo Control Board Rev.2.csv, Smart Servo Control Board Rev.2.kicad_pcb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]
2025-04-13 Lugre and various tests
    [Smart Servo Control Board Rev.2.kicad_pcb, Smart Servo Control Board Rev.2.kicad_sch]
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2025-09-19 codice e scheda a buon punto
    [Smart Servo Control Board Rev.1-B_Cu.gbl, Smart Servo Control Board Rev.1-B_Mask.gbs, Smart Servo Control Board Rev.1-B_Paste.gbp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]
2025-10-01 incontro prof
    [Smart Servo Control Board Rev.1.csv]
2026-03-15 thesis update
    [MG996R_data.xlsx, STM32F103C8T6 minimum board.kicad_pcb, STM32F103C8T6 minimum board.kicad_sch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]

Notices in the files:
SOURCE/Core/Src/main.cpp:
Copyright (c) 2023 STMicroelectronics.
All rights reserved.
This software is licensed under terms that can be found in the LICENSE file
